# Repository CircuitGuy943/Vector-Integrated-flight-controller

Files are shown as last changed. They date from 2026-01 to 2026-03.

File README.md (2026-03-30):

I am currently trying to build my own drone from scratch, and slowly replace every component with my own, from creating fully custom PCBs for the flight controller or ESCs, to making a 3D printed drone chassis etc etc. And this is the fully fledged, multi functional, cool-looking flight controller. I present to you:

# *SABRE!*




For one of my biggest projects yet I designed a jack of all trades custom flight controller board. It also comes with custom firmware, or if possible compatibility with betaflight or other FC firmware out there. At it's core are two PCBs arranged in a stackup with the "top" and "bottom" sections. The two PCBs connect through the common 2.54mm pitch headers and stack on top of eachother and each serve to provide enough space for all the components and separate the sensitive digital components from the electromagnetic potential of the motor power rails. The bottom board houses E-Fuse protection and an INA226 current monitor to protect the boards, including powered FPV feed with the AT7456E and TX5813, accompanied by four MOSFET powered 12V LED strip channels. The top booard houses a powerful STM32F765VGT CPU which will, *fingers crossed,* be more than enough to run automatic flight levelling software quickly enough to not crash. Followed by a micro SD card slot for storing flight telemetry, programmable DIP switched for easy settings, BNO08x 9-DOF sensor module, segment display and pushbuttons for easy configuration without needing to reupload code and a BMP580 barometic sensor. More than I (or you) will ever need to fly a 4 blade, 1KG piece of PETG plastic :)

### Bottom Board:

Half of the bottom PCB houses the power delivery circuitry. This includes a dedicated TPS259850 chip, or an E-Fuse, required protection option for a drone that operates at around 20A sustained and 40A current peaks. Thanks to it's extremely low RDS on, basically no power is wasted, and it trips the circuit in a matter of microseconds when too much current is detected, which makes it extremely useful for a drone full of sensitive circuitry, compared to a traditional wire fuse. Followed by that is an INA226 chip, this aims to precisely monitor the current consumption of the entire drone, helping to predict flight times and efficiently manage battery health, through the use of a shunt resistor sized to the expected current draw. The current planes are optimized to make proper use of the different outer and inner layer thicknesses and properly distribute current with minimal heat up.

The other part of the bottom PCB houses the RF circuitry for the FPV system LED drivers togethor with power regulators that power the 12V rail for the LED drivers and the 5V rail for the FPV system and other 5V chips. The 12V power regulator (TPS55289) and the 5V regulator (TPS63070) both use the safest and most reliable layouts possible and are positioned to spatially divide the high ~32A currents on the bottom power distribution circuitry from the rest of the bottom board, a slide switch also controls the power supply to the TX5813 module, as this consumes the most out of the other board circuitry, at about ~200mA, this should help to increase flight time by cutting wasted power when the FPV function isn't being used. CSD16340 MOSFETS also serve to drive 4 seperate 12V LED strip channels, these I plan to connect to LED strips and create cool illuminations off of my drone.

The RF circuitry benefits from an impedance accurate JLC-3313 stackup and use of coplanar waveguide routing with via fencing, tearsrops and udnerpad via router to insure the least impedance mismatch possible. The actual RF system is composed of an external camera connector, or simple pin header (capable of reading almost any FPV camera such as the Caddx Ant Lite). The video signal is then passed through a meticulously routed 75ohm impedance matched trace into a MAX7456EUI (Or a newer drop in AT7456E replacement, pin to pin compatible), this module serves to inject an OSD (On screen display) into the video feed through communication with the STM32 MCU for easy sending of telemtry data like battery voltage, speed, altitude etc. The output from the OSD injection chip is then routed through another impedance matched trace with SAG correction into the video input of the TX5813. This modules handles the complicated circuitry of converting the video feed (~6MHz) into a radio signal of ~5.8GHz. That RF is then routed even more carefuly for the short length (~8mm) of the SMA launch into the SMA connector then into any respective 5.8GHz FPV antenna. (I also have a complemintary project for a 5.8GHz FPV reciever in another repository)

### Top Board:

Flying the drone is an STM32F765VGT CPU with up to 216MHz clock speed, hopefully resulting in almost perfect drone levelling and flight, on the other side of the board is also a USB C receptacle for programming the STM CPU, and powering the board while doing so (everything except the motors, of course, I also included diodes to prevent power backfeed). Close by is a BNO08x 9-DOF accelerometer, gyroscope and magnetometer, complete with an integrated 32-bit ARM Cortex-M0+ for quick sensor fusion with pre built firmware (meaning I have to code waaaay less :D). Motor PWM outputs for the ESCs also connected directly to PWM channels on the STM32 and two solder bridgeable connections to allow me to use the 5V supply from the ESCs in case my 5V regulator doesn't function properly under load (I've had bad experience with voltage regulators). Several voltage indicator LEDs are also placed near the USB C port at the back. Then there is also an UART FPC port designed to connect to a separate GPS board (large board for good GPS recieving power, check my other repositories) on the left side of the board. A 7 segment, 4 digit bitbanged display and several tactile pushbottoms also occupy the centre of the board, quite useless but they might be useful in changing more accute settings without having to reupload firmware every time. A micro SD card also connects through 4 channel SPI to STM32, I plan to use this to store settings or flight telemetry information that I could analyze while debugging. Powering all that is a 3.3V regulator (LMR51430XF), simplest (and therefore most reliable) I could find. And several other breakout headers for power/functionality. PWM inputs from the radio remote is recieved through a 3x8 header pinout designed for my specific radio reciever module.

(For BP reviewer: Btw, the two boards will be connected and bought as one piece from JLC, then I will cut them apart and stack them, I just ran out of time to do that, there's also quite a bit off polishing off to do like doing Fusion renders but I've also run out of time, so the project would be a bit more polished and it will be but not before the BP deadline. 3D file of board is also too big (over 100MB) to upload to GitHub)

## Features:
- Fully integrated design:
	- Custom firmware uploadable
	- Power distribution and control in one place
	- Dual stacked PCB design
 	- No screw, no wire inter board connection

- Power
	- Extremely low RDS protection e-Fuse (us trip time)
 	- INA226 current and voltage monitoring
  	- Backup/calibration voltage divider monitoring
  	- Fully optimized current planes, 40A+ capability
  	- Firmware built in battery management and flight warning system
  	- Meticulously designed 5V, 12V and 3.3V switching voltage regulators
  	- Backup ESC 5V supply availible
  	- LED indicators for power rail status
  	- 4 channel driver for 12V LED strips
  	- Power switch for TX5813 module for longer flight times

- Fully integrated FPV support
	- MAX7456/AT7456E OSD injection into FPV feed
	- Channel switch ability
	- TX5813 RF launch module
	- Accurate and reliable RF design
 	- Designed for impedance matched JLC 3313 stackup
 
- Flight Control
	- USB C programming connection 
	- Powerful STM32F765VGT CPU
 	- MicroSD card slot (For inflight telemtry storage)
  	- Programmable DIP switches
  	- Display/pushbuttons for setting adjustment without code reupload
  	- BNO08x 9-DOF sensor module with built in sensor fusion
  	- BMP580 Barometric sensor
  	- UART FPC connection for external GPS board
  	- Extra power and I2C debug headers
  	- 7 input PWM channels
  	- 4 ESC output PWM channels

## PCB
This is the PCB, with L1 to L4 Layers, silkscreen for both layers and an all layers view

PCB PCB 2 PCB 3 
PCB 4 PCB 5 PCB 6
PCB 7 PCB 8 PCB 9 

And here is the schematic

Schematic1
Schematic2
Schematic3

## 3D render
Here is also a 3D render to show off the PCB :)

Render1

## Firmware Overview
I've included some basic firmware (**untested**) that should get the TFT display working out of the box with a quick upload from arduino IDE

## BOM:
The BOM list for the actual PCB components is in the BOM folder section and here is also a BOM list for all the other components I plan to buy for this:

- PCB             $378.08		
- Antenna         $7.77      https://www.aliexpress.com/item/1005006153683653.html		
- 90 degree SMA   $4.51      https://www.aliexpress.com/item/1005005665998117.html						
- TX5813 module   $15.82     https://www.aliexpress.com/item/1005011698073364.html
											
Total			      $406.18

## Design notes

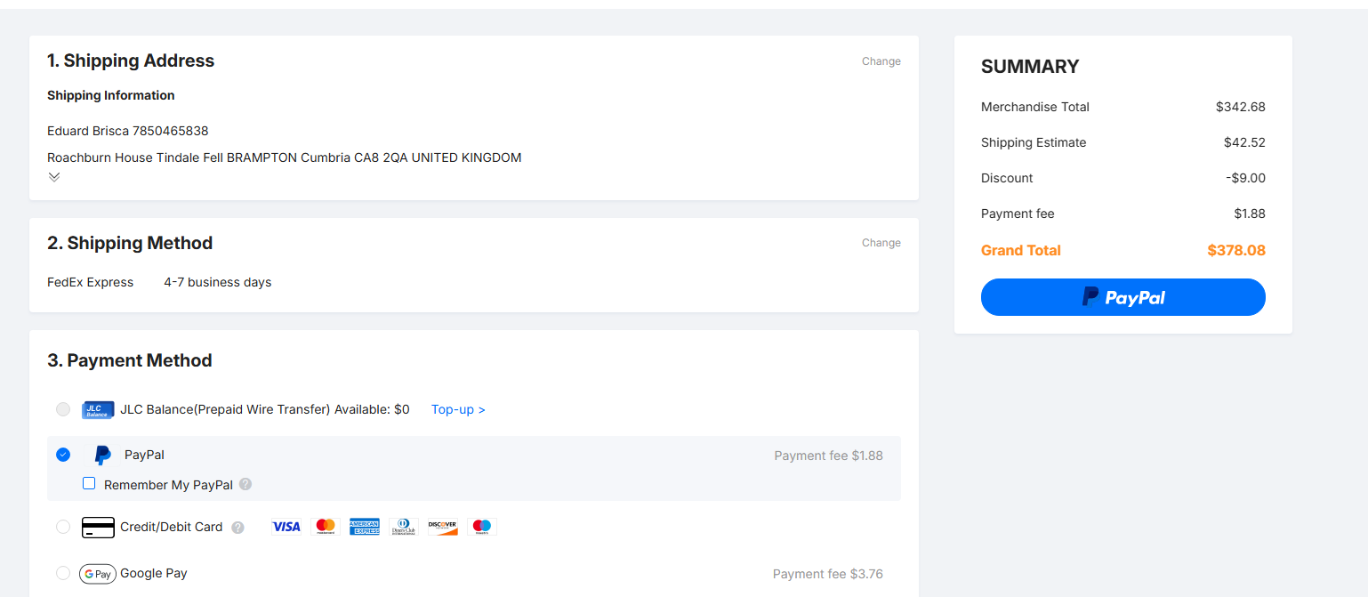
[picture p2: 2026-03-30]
Pictures/cart2.png

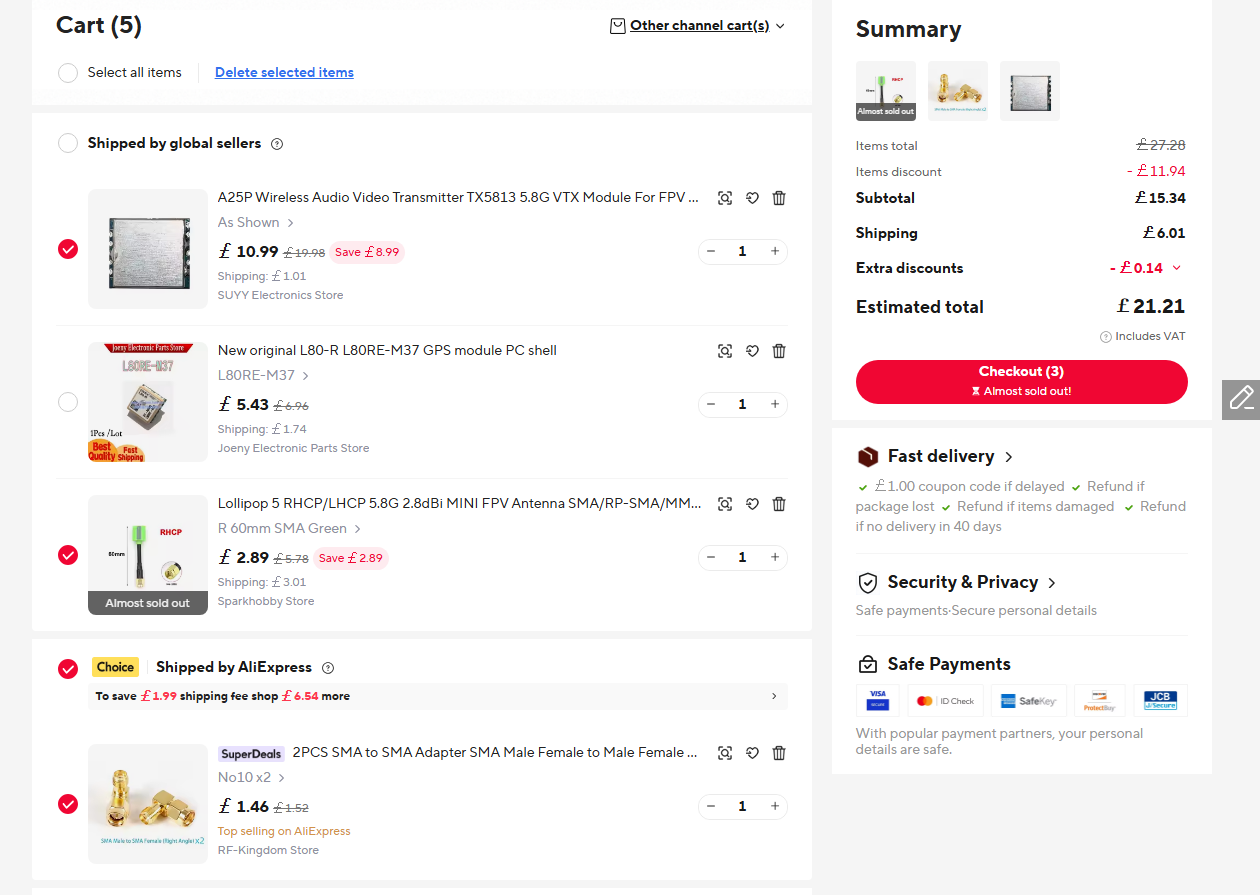
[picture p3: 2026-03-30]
Pictures/cart1.png

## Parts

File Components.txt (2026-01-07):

SENSORS
1. 9 Axis DOF IMU - BNO085. Sensor fusion integrated into the chip, reduces the need for MCU Kalman filters etc and therefore reduces MCU load and increases reliability
2. Barometer for altitude / temperature - BMP580. Can be connected straight to MCU or through a passthrough for “Environmental Sensors” through the BNO085, this is harder to implement but it may simplify circuitry use less I2C lines.
3. STM32 processor. Which one? Needs to be dual core

CONTROL
1. GPIO PWM outputs connected to 4 (more if there is space) groups of 3 pin headers for the ESCs, backup 5V power will also be taken from here as ESCs also step-down power to 5V. Located preferably in a symmetric position or spread out symmetrically so all the wires are extended the same.
2. PWM Inputs from the Radio Receiver (6 groups of also 3 pin headers, more if there is space and GPIO availability). These must OUTPUT 5V as well because the receiver needs a voltage input to function, unlike the ESCs that make their own.

POWER
1. USB C port connection on the back of the board
2. Female XT60 power connector with appropriate step down for MCU and sensors (Not LDO as components will likely consume too much current for too high a step down from ~14V)
3. Dual connection with diodes to both the ESC power outputs but also a voltage reducer like LDO or buck reducer on the USB C for redundancy if the LDO/buck dies.
4. Each side of the board will also have 2 (Maybe more if there's space) XT60 connectors powering the ESCs/motors

CAMERA SUPPORT
1. Caddx Ant (Lite) camera
2. 75-ohm impedance matched trace from JST-SH 1.0?mm connector to VID_IN of OSD Injector
3. MAX7456 OSD injector connected through communication protocol to MCU
4. MAC7456 VID_OUT connected through another 75-ohm impedance matched trace to TX5813 VID_IN
5. TX5813 SMD VTX + necessary support electronics + switch for on/off as VTX is very power hungry
6. 50-ohm impedance matched / ground trace from ANTENNA pad to an SMA connector
7. Antenna
Plus, appropriate ground plane and distances from other electronics such as MCU and switching regulators

OTHER
1. 12V LED control with up to 200mA+ of power available from GPIO.
2. SD Card module also placed wherever best, far away from the VTX module and preferably close to the MCU
3. I2C and SPI output headers for any future addition of sensors/logging/modules
4. 4 segment display (3 if not enough GPIO) plus a few tactile buttons (again GPIO limited) to allow easy tweaking of PID control values and other settings without the need for reupload of code.
5. Voltage divider for voltage sensing.
6. Voltage and current sensing on main power rail

USE 0805 LEDS FOR BASIC COMPONENT

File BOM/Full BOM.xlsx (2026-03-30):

BOM LIST | Pounds | Dollars
PCB |  | $378.08
Antenna | £5.80 | $7.77 | https://www.aliexpress.com/item/1005006153683653.html
90 degree SMA | £3.37 | $4.51 | https://www.aliexpress.com/item/1005005665998117.html
RX5808 module |  | $15.82 | https://www.aliexpress.com/item/1005011698073364.html
Total |  | $406.18

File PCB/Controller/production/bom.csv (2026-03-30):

Designator | Footprint | Quantity | Value | LCSC Part #
BUZ1 | BUZ-SMD_L9.0-W9.0-P8.00-LS9.3 | 1 | CPT-9019S-SMT-TR | C95163
C1 | 0603 | 1 | 0.1uF
C10, C57, C58 | 0402 | 3 | 2.2uF
C11, C14, C15, C2, C27, C29, C30, C31, C32, C33, C34, C36, C37, C38, C41, C44, C45, C46, C47, C48, C49, C50, C51, C63, C64, C67, C78 | 0402 | 27 | 100nF
C12, C13 | 0603 | 2 | 22uF
C16, C19, C20, C21, C22 | 0402 | 5 | 22uF
C17 | 0402 | 1 | 4.7uF
C18, C28 | 0402 | 2 | 22nF
C23 | 0402 | 1 | 3300pF
C24 | 0402 | 1 | 330pF
C25 | CAP-SMD_BD6.3-L6.6-W6.6-LS7.2-FD | 1 | 47uF | C970677
C3, C6 | 0603 | 2 | 10uF
C35, C43, C56, C68, C77 | 0402 | 5 | 10uF
C39, C40, C60, C61 | 0402 | 4 | 20pF
C4, C5 | 0805 | 2 | 10uF
C42, C74 | CAP-SMD_BD4.0-L4.3-W4.3-FD-LS5.3 | 2 | RVT1C220M0405_C3356_22uF | C3356
C52, C53, C54, C55, C65 | 0402 | 5 | 1uF
C59, C62 | 0402 | 2 | 6.8pF
C66 | 1210 | 1 | 100uF
C69, C75, C76 | 0402 | 3 | 0.1uF
C7, C8, C9 | 0805 | 3 | 22uF
C70 | 0402 | 1 | 15nF
C71 | 0402 | 1 | 3.3nF
C72 | 0402 | 1 | 10nF
C73 | 0402 | 1 | 150pF
C79 | 1206 | 1 | 22uF
CARD2 | TF-SMD_TF-01A | 1 | TF-01A | C91145
CN1 | AMASS_XT60PW-M_1x02_P7.20mm_Horizontal | 1 | XT60PW_M | C98732
CN2, CN4, CN5, CN6 | AMASS_XT60PW-F_1x02_P7.20mm_Horizontal | 4 | XT60PW_F | C428722
D1, D2, D3, D4, D5, D6 | D_SMA | 6 | SS34
GPS | FPC-SMD_6P-P0.50_XUNPU_FPC-05F-6PH20 | 1 | FPC-05F-6PH20 | C2856796
J1 | PinHeader_2x07_P2.54mm_Vertical | 1 | Conn_02x07_Odd_Even
J10, J5, J6, J7, J8 | PinHeader_1x03_P2.54mm_Vertical | 5 | Conn_01x03_Pin
J12 | PinHeader_2x02_P2.54mm_Vertical | 1 | Conn_02x02_Top_Bottom
J13, J18 | PinHeader_1x14_P2.54mm_Vertical | 2 | Conn_01x14_Pin
J14, J19 | PinHeader_1x06_P2.54mm_Vertical | 2 | Conn_01x06_Pin
J15, J20 | PinSocket_1x14_P2.54mm_Vertical | 2 | Conn_01x14_Socket
J16, J17 | PinSocket_1x06_P2.54mm_Vertical | 2 | Conn_01x06_Socket
J2, J9 | PinHeader_1x02_P1.00mm_Vertical | 2 | Conn_01x02_Pin
J21 | PinHeader_2x04_P2.54mm_Vertical | 1 | Conn_02x04_Odd_Even
L1 | IND-SMD_L4.0-W4.0-A | 1 | XFL4020-152MEC | C3033018
L2 | L0603 | 1 | FCM1608KF-601T03 | C141723
LED1 | LED-SEG-TH_14P-L32.2-W10.2-P2.54-S7.62-BL | 1 | FJ2481CH | C10707
LED11, LED12, LED13, LED14, LED15, LED16, LED2, LED9 | LED0603-RD | 8 | KT-0603YG | C2289
LED3, LED8 | LED0603-RD | 2 | KT-0603R | C2286
LED4, LED5, LED6, LED7 | LED0603-R-RD_WHITE | 4 | KT-0603W | C2290
Q1, Q2, Q3, Q5 | VSON-CLIP-8_L3.3-W3.3-P0.65-BL | 4 | CSD16340Q3 | C47616
Q10, Q7, Q8, Q9 | SOT-23_L2.9-W1.3-P1.90-LS2.4-BR | 4 | LBSS138LT1G | C8490
R1, R2 | 0402 | 2 | 5.1K
R10 | 0402 | 1 | 22.1K
R100, R103, R104, R16, R99 | 0402 | 5 | 4.7K
R101 | 0603 | 1 | 10K
R102, R12, R20, R22, R27, R28, R29, R30, R31, R34, R35, R49, R58, R6, R61, R62, R63, R64, R65, R66, R7, R88, R96, R97, R98 | 0402 | 25 | 10K
R11, R33 | 0402 | 2 | 68K
R13, R14 | 0402 | 2 | 56K
R15, R52 | 0402 | 2 | 24K
R17, R18, R19, R21, R36, R37, R38, R39, R4, R40, R41, R42, R43, R44, R45, R46, R47, R48, R60, R67, R68, R69, R76, R77, R82 | 0402 | 25 | 220
R23 | 0402 | 1 | 150K
R24 | 0402 | 1 | 47K
R25, R26, R55 | 0402 | 3 | 2.2K
R3 | R2725 | 1 | HOLR2725D-4W-2MR-1% | C500746
R32, R54, R85, R86, R87 | 0402 | 5 | 1K
R5, R72, R73, R74, R75 | 0402 | 5 | 680
R50 | 0402 | 1 | 160
R51 | 0402 | 1 | 1.1K
R53 | 0402 | 1 | 1.5K
R56 | 0402 | 1 | 50K
R78 | 0402 | 1 | 100
R8, R9 | 0402 | 2 | 100K
R83, R84 | 0603 | 2 | 75
SW1, SW11, SW12, SW2, SW3, SW4, SW5, SW6, SW7, SW8, SW9 | SW-SMD_L3.9-W3.0-P4.45 | 11 | TS-1088-AR02016 | C720477
SW10, SW14 | SW-SMD_DSIC03LSGET | 2 | DSIC03LSGET | C57453
SW13 | SW-SMD_MK-11C04-G013 | 1 | MK-11C04-G013 | C778185
U1 | LQFP-100_14x14mm_P0.5mm | 1 | STM32F765VGTx
U10 | MC7RE | 1 | ~
U11 | VSSOP-10_L3.0-W3.0-P0.50-LS4.9-BL | 1 | INA226AQDGSRQ1 | C2653835
U12 | SOT-23-6 | 1 | LMR51430XF
U13 | CAP-SMD_BD6.3-L6.6-W6.6-LS7.2-FD-1 | 1 | 100uF | C970685
U14 | LGA-8_BME280_BL | 1 | BME280 | C92489
U15 | CRYSTAL-SMD_4P-L3.2-W2.5-BL | 1 | S322527M20PF10PPM | C7420779
U16 | VQFN-20_L4.5-W3.5-P0.50-BL-EP | 1 | TXB0108RGYR | C194701
U17 | TX5813 | 1 | TX5813
U19 | QFN-26_L5.0-W4.5_TPS259850RQPR | 1 | TPS259850RQPR | C6290347
U2 | LGA-28_L5.2-W3.8-P0.50-BL-1 | 1 | BNO080 | C717991
U20 | SO-8_L4.9-W3.9-P1.27-LS6.0-BL | 1 | LD1117D33TR | C2971297
U3 | LGA-10_L2.0-W2.0-P0.50-TL_BMP580 | 1 | BMP580 | C22391138
U4 | IND-SMD_L5.5-W5.3 | 1 | XAL5050-562MEC | C7305309
U5 | HTSSOP-28_L9.7-W4.4-P0.65-LS6.4-BL-EP5.5 | 1 | MAX7456EUI | C5346361
U6 | SMA-TH_SMA-KWE_C7498154 | 1 | SMA_Conn | C7498154
U7 | VQFN-21_L5.0-W3.0-P0.50-TL | 1 | TPS55289RYQR | C5942077
U8 | IND-SMD_L7.5-W7.2-1 | 1 | XAL7070-472MEC | C3911513
U9 | VQFN-15_L3.0-W2.5-P0.50-BL | 1 | TPS630701RNMT | C181473
USB1 | USB-C-SMD_TYPE-C16PIN_C668624 | 1 | TYPE-C 16P(073) | C668624
X1 | CRYSTAL-SMD_4P-L3.2-W2.5-BL | 1 | X322525MOB4SI | C9006
X2 | FC-135R_L3.2-W1.5 | 1 | Q13FC1350000400 | C32346

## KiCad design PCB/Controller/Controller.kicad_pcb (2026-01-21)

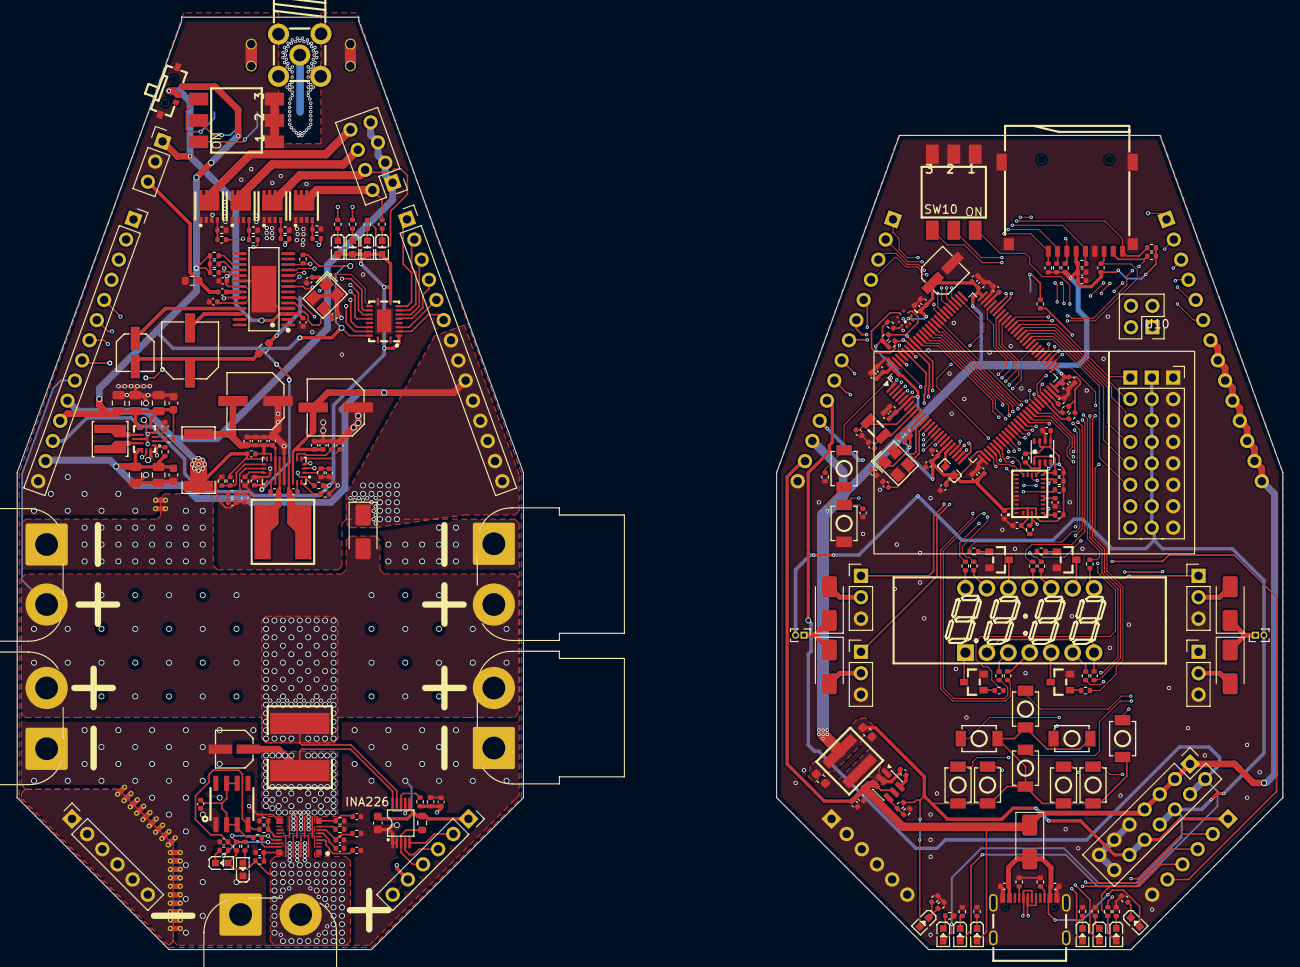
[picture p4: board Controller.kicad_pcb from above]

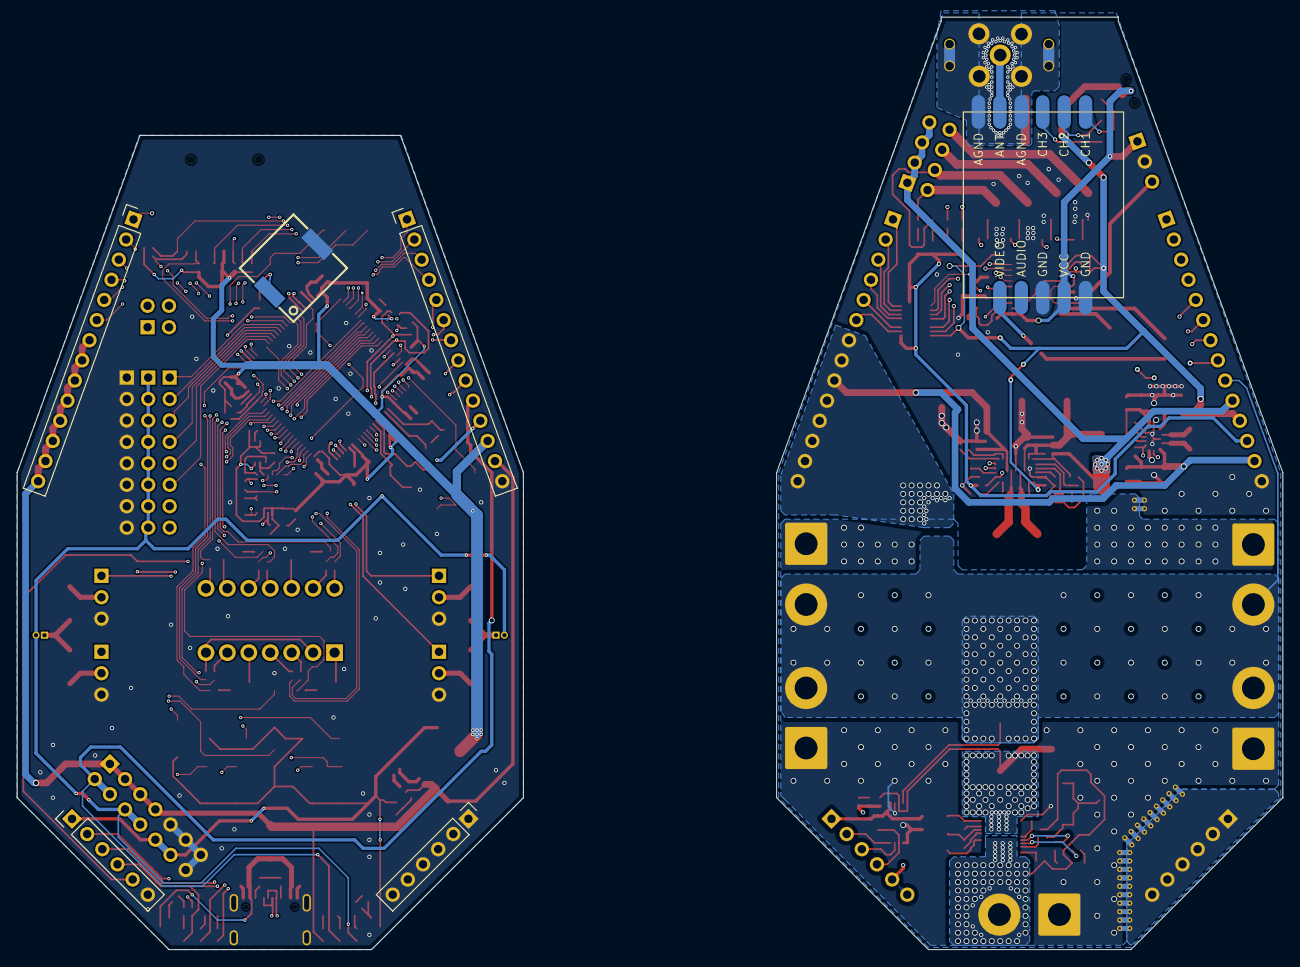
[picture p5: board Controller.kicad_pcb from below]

Board: 4 copper layers, 150.0 x 110.5 mm, 284 parts (6 on the bottom side), 219 nets.

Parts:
BUZ1: CPT-9019S-SMT-TR; BUZ-SMD_L9.0-W9.0-P8.00-LS9.3
C1: 0.1uF; C_0603_1608Metric
C2, C11, C14, C15, C26, C27, C29, C30, C31, C32, C33, C34, C36, C37, C38, C41, C44, C45, C46, C47, C48, C49, C50, C51, C63, C64, C67, C78: 100nF; C_0402_1005Metric
C3, C6: 10uF; C_0603_1608Metric
C4, C5: 10uF; C_0805_2012Metric
C7, C8, C9: 22uF; C_0805_2012Metric
C10, C57, C58: 2.2uF; C_0402_1005Metric
C12, C13: 22uF; C_0603_1608Metric
C16, C19, C20, C21, C22: 22uF; C_0402_1005Metric
C17: 4.7uF; C_0402_1005Metric
C18, C28: 22nF; C_0402_1005Metric
C23: 3300pF; C_0402_1005Metric
C24: 330pF; C_0402_1005Metric
C25: 47uF; CAP-SMD_BD6.3-L6.6-W6.6-LS7.2-FD
C35, C43, C56, C68, C77: 10uF; C_0402_1005Metric
C39, C40, C60, C61: 20pF; C_0402_1005Metric
C42, C66, C74: RVT1C220M0405_C3356_22uF; CAP-SMD_BD4.0-L4.3-W4.3-FD-LS5.3
C52, C53, C54, C55, C65: 1uF; C_0402_1005Metric
C59, C62: 6.8pF; C_0402_1005Metric
C69, C75, C76: 0.1uF; C_0402_1005Metric
C70: 15nF; C_0402_1005Metric
C71: 3.3nF; C_0402_1005Metric
C72: 10nF; C_0402_1005Metric
C73: 150pF; C_0402_1005Metric
CN1: XT60PW_M; AMASS_XT60PW-M_1x02_P7.20mm_Horizontal
CN2, CN4, CN5, CN6: XT60PW_F; AMASS_XT60PW-F_1x02_P7.20mm_Horizontal
Card2: TF-01A; TF-SMD_TF-01A
D1, D2, D3, D4, D5, D6: SS34; D_SMA
J1: Conn_02x07_Odd_Even; PinHeader_2x07_P2.54mm_Vertical
J2, J9: Conn_01x02_Pin; PinHeader_1x02_P1.00mm_Vertical
J5, J6, J7, J8, J10: Conn_01x03_Pin; PinHeader_1x03_P2.54mm_Vertical
J12: Conn_02x02_Top_Bottom; PinHeader_2x02_P2.54mm_Vertical
J13, J18: Conn_01x14_Pin; PinHeader_1x14_P2.54mm_Vertical
J14, J19: Conn_01x06_Pin; PinHeader_1x06_P2.54mm_Vertical
J15, J20: Conn_01x14_Socket; PinSocket_1x14_P2.54mm_Vertical
J16, J17: Conn_01x06_Socket; PinSocket_1x06_P2.54mm_Vertical
J21: Conn_02x04_Odd_Even; PinHeader_2x04_P2.54mm_Vertical
L1: XFL4020-152MEC; IND-SMD_L4.0-W4.0-A
L2: FCM1608KF-601T03; L0603
LED1: FJ2481CH; LED-SEG-TH_14P-L32.2-W10.2-P2.54-S7.62-BL
LED2, LED9, LED11, LED12, LED13, LED14, LED15, LED16: KT-0603YG; LED0603-RD
LED3, LED8: KT-0603R; LED0603-RD
LED4, LED5, LED6, LED7: KT-0603W; LED0603-R-RD_WHITE
NT1, NT7, NT8, NT9, NT10, NT10#2, NT10#3, NT10#4, NT11, NT11#2, NT11#3, NT11#4, NT12, NT13, NT13#2, NT13#3, NT14, NT15, NT15#2, NT15#3, NT16: NetTie_2; NetTie-2_THT_Pad0.3mm
NT2, NT17: NetTie_2; NetTie-2_THT_Pad1.0mm
Q1, Q2, Q3, Q5: CSD16340Q3; VSON-CLIP-8_L3.3-W3.3-P0.65-BL
Q7, Q8, Q9, Q10: LBSS138LT1G; SOT-23_L2.9-W1.3-P1.90-LS2.4-BR
R1, R2: 5.1K; R_0402_1005Metric
R3: HOLR2725D-4W-2MR-1%; R2725
R4, R17, R18, R19, R21, R36, R37, R38, R39, R40, R41, R42, R43, R44, R45, R46, R47, R48, R60, R67, R68, R69, R76, R77, R82: 220; R_0402_1005Metric
R5, R72, R73, R74, R75: 680; R_0402_1005Metric
R6, R7, R12, R20, R22, R27, R28, R29, R30, R31, R34, R35, R49, R58, R61, R62, R63, R64, R65, R66, R88, R96, R97, R98, R102: 10K; R_0402_1005Metric
R8, R9: 100K; R_0402_1005Metric
R10: 22.1K; R_0402_1005Metric
R11, R33: 68K; R_0402_1005Metric
R13, R14: 56K; R_0402_1005Metric
R15: MS122WF100MT4E; R2512
R16, R99, R100, R103, R104: 4.7K; R_0402_1005Metric
R23: 150K; R_0402_1005Metric
R24: 47K; R_0402_1005Metric
R25, R26, R55: 2.2K; R_0402_1005Metric
R32, R54, R85, R86, R87: 1K; R_0402_1005Metric
R50: 160; R_0402_1005Metric
R51: 1.1K; R_0402_1005Metric
R52: 48K; R_0402_1005Metric
R53: 1.5K; R_0402_1005Metric
R56: 50K; R_0402_1005Metric
R78: 100; R_0402_1005Metric
R83, R84: 75; R_0603_1608Metric
R101: 10K; R_0603_1608Metric
SW1, SW2, SW3, SW4, SW5, SW6, SW7, SW8, SW9, SW11, SW12: TS-1088-AR02016; SW-SMD_L3.9-W3.0-P4.45
SW10, SW14: DSIC03LSGET; SW-SMD_DSIC03LSGET
SW13: MK-11C04-G013; SW-SMD_MK-11C04-G013
U1: STM32F765VGTx; LQFP-100_14x14mm_P0.5mm
U2: BNO080; LGA-28_L5.2-W3.8-P0.50-BL-1
U3: BMP580; LGA-10_L2.0-W2.0-P0.50-TL_BMP580
U4: XAL5050-562MEC; IND-SMD_L5.5-W5.3
U5: MAX7456EUI; HTSSOP-28_L9.7-W4.4-P0.65-LS6.4-BL-EP5.5
U6: SMA_Conn; SMA-TH_SMA-KWE_C7498154
U7: TPS55289RYQR; VQFN-21_L5.0-W3.0-P0.50-TL
U8: XAL7070-472MEC; IND-SMD_L7.5-W7.2-1
U9: TPS630701RNMT; VQFN-15_L3.0-W2.5-P0.50-BL
U10: MC7RE
U11: INA226AQDGSRQ1; VSSOP-10_L3.0-W3.0-P0.50-LS4.9-BL
U12: LMR51430; SOT-23-6
U13, U18: 100uF; CAP-SMD_BD6.3-L6.6-W6.6-LS7.2-FD-1
U14: BME280; LGA-8_BME280_BL
U15: S322527M20PF10PPM; CRYSTAL-SMD_4P-L3.2-W2.5-BL
U16: TXB0108RGYR; VQFN-20_L4.5-W3.5-P0.50-BL-EP
U17: TX5813
U19: TPS259850RQPR; QFN-26_L5.0-W4.5_TPS259850RQPR
U20: LD1117D33TR; SO-8_L4.9-W3.9-P1.27-LS6.0-BL
USB1: TYPE-C 16P(073); USB-C-SMD_TYPE-C16PIN_C668624
X1: X322525MOB4SI; CRYSTAL-SMD_4P-L3.2-W2.5-BL
X2: Q13FC1350000400; FC-135R_L3.2-W1.5

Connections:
+3.3V: C12.2, C13.2, C29.1, C30.1, C32.2, C33.2, C34.2, C42.1, C43.1, C45.1, C46.1, C47.1, C48.1, C49.1, C50.1, C51.1, C52.1, C53.1, C54.1, C55.1, C56.1, C64.1, C65.1, C67.1, C68.1, Card2.4 (VDD), J1.10, J1.12, J13.12, J14.1, L2.2, LED16.2 (A), R6.2, R9.2, R25.2, R26.2, R27.1, R58.2, R61.2, R62.2, R63.2, R64.2, R65.2, R66.2, R96.1, R97.1, R98.1, R99.1, R100.1, R102.1, R103.2, R104.2, SW1.2, SW2.2, SW3.2, SW4.2, SW5.2, SW6.2, SW7.2, SW8.2, SW9.2, SW12.1, U1.6 (VBAT), U1.11 (VDD), U1.20 (VREF+), U1.27 (VDD), U1.50 (VDD), U1.75 (VDD), U1.100 (VDD), U2.3 (VDD), U2.5 (PS1), U2.28 (VDDIO), U3.1 (VDDIO), U3.10 (VDD), U4.2, U14.2 (CSB), U14.6 (VDDIO), U14.8 (VDD)
+3.3V_B: C1.2, J15.12, J16.1, LED4.1 (A), LED5.1 (A), LED6.1 (A), LED7.1 (A), R28.1, R101.2, U11.6 (VS+), U16.2 (VCCA), U16.10 (OE)
+5V: J1.6, J1.8, J2.2, J9.2, J13.11, LED15.2 (A), U10.17 (5V), U10.18 (5V), U10.19 (5V), U10.20 (5V), U10.21 (5V), U10.22 (5V), U10.23 (5V), U10.24 (SBUS3)
+5V_B: C6.2, C7.2, C8.2, C9.2, C17.2, J15.11, R8.2, R85.2, R86.2, R87.2, R88.2, SW13.1, U7.18 (VCC), U9.5 (FB), U9.7 (VOUT), U16.19 (VCCB)
+12V: J1.2, J1.4, J13.10, LED14.2 (A)
+12V_B: C26.1, J15.10, J21.1, J21.3, J21.5, J21.7, R11.2, R15.2, U7.13 (ISN)
BMP580_INT: R102.2, U1.96 (PB9), U3.7 (INT)
BNO580_BOOTN: R27.2, U1.34 (PB0), U2.4 (BOOTN)
BNO580_CSN: U1.77 (PA15), U2.18 (H_CSN)
BNO580_INTN: R98.2, U1.33 (PC5), U2.14 (H_INTN)
BNO580_MISO: U1.30 (PA6), U2.20 (H_SDA/H_MISO/TX)
BNO580_MOSI: U1.31 (PA7), U2.17 (SA0/H_MOSI)
BNO580_NRST: R97.2, U1.32 (PC4), U2.11 (NRST)
BNO580_SCLK: U1.29 (PA5), U2.19 (H_SCL/SCK/RX)
BNO580_WAKE: R96.2, U1.35 (PB1), U2.6 (PS0/WAKE)
BOOT: R22.1, SW12.2, U1.94 (BOOT0)
BOOT1: C14.2, U7.8 (SW1), U8.2
BOOT2: C15.2, U7.10 (SW2), U8.1
BUTTON_DECREASE: SW4.1, U1.39 (PE9)
BUTTON_F1: SW6.1, U1.41 (PE11)
BUTTON_F2: SW7.1, U1.42 (PE12)
BUTTON_F3: SW8.1, U1.43 (PE13)
BUTTON_F4: SW9.1, U1.51 (PB12)
BUTTON_INCREASE: SW3.1, U1.38 (PE8)
BUTTON_LEFT: SW1.1, U1.36 (PB2)
BUTTON_OK: SW5.1, U1.40 (PE10)
BUTTON_RIGHT: SW2.1, U1.37 (PE7)
BUZZER: R78.1, U1.53 (PB14)
DIP_1: SW10.6 (B1), U1.52 (PB13)
DIP_2: SW10.5 (B2), U1.54 (PB15)
DIP_3: SW10.4 (B3), U1.55 (PD8)
DISP_A: R41.2, U1.87 (PD6)
DISP_B: R44.2, U1.86 (PD5)
DISP_C: R38.2, U1.85 (PD4)
DISP_D: R39.2, U1.84 (PD3)
DISP_D2D1: R45.2, U1.58 (PD11)
DISP_DIG1: R46.1, U1.91 (PB5)
DISP_DIG2: R48.1, U1.90 (PB4)
DISP_DIG3: R36.1, U1.89 (PB3)
DISP_DIG4: R47.1, U1.88 (PD7)
DISP_DP: R40.2, U1.67 (PA8)
DISP_E: R37.2, U1.72 (PA13)
DISP_F: R42.2, U1.69 (PA10)
DISP_G: R43.2, U1.68 (PA9)
EXTRA_I2C_EN: J12.4, U1.44 (PE14)
EXTRA_I2C_INT: J12.3, U1.45 (PE15)
EXTRA_I2C_SCL: J12.1, R103.1, U1.46 (PB10)
EXTRA_I2C_SDA: J12.2, R104.1, U1.47 (PB11)
GND: BUZ1.2 (-), C10.2, C12.1, C13.1, C29.2, C30.2, C31.1, C32.1, C33.1, C34.1, C35.2, C42.2, C43.2, C45.2, C46.2, C47.2, C48.2, C49.2, C50.2, C51.2, C52.2, C53.2, C54.2, C55.2, C56.2, C57.1, C58.1, C59.2, C60.2, C61.1, C62.2, C63.2, C64.2, C65.2, C67.2, C68.2, C77.2, C78.2, Card2.6 (VSS), Card2.10 (GND), Card2.11 (GND), Card2.12 (GND), Card2.13 (GND), J1.9, J1.11, J1.13, J1.14, J5.3, J6.3, J7.3, J8.3, J13.14, J14.6, J19.1, J19.2, J19.3, J19.4, J19.5, J19.6, Q7.2 (S), Q8.2 (S), Q9.2 (S), Q10.2 (S), R1.2, R2.2, R4.2, R5.2, R10.2, R22.2, R72.2, R73.2, R74.2, R75.2, R76.2, R77.2, R82.2, SW10.1 (A1), SW10.2 (A2), SW10.3 (A3), SW11.1, U1.10 (VSS), U1.19 (VSSA), U1.26 (VSS), U1.49 (VSS), U1.74 (VSS), U1.99 (VSS), U2.2 (GND), U2.25 (GND), U2.26 (XOUT32/CLKSEL1), U3.3 (VSS), U3.5 (SDO), U3.6 (CSB), U3.8 (VSS), U3.9 (VSS), U10.9 (GND), U10.10 (GND), U10.11 (GND), U10.12 (GND), U10.13 (GND), U10.14 (GND), U10.15 (GND), U10.16 (SBUS2), U12.1 (GND), U14.1 (GND), U14.7 (GND), USB1.1 (SHELL), USB1.2 (SHELL), USB1.3 (SHELL), USB1.4 (SHELL), USB1.A1B12 (GND), USB1.B1A12 (GND), X1.2 (GND), X1.4 (GND)
GND_B: C2.2, C3.1, C4.1, C5.1, C6.1, C7.1, C8.1, C9.1, C16.1, C17.1, C18.1, C19.1, C20.1, C21.1, C22.1, C23.1, C24.1, C25.1, C27.1, C36.1, C37.1, C38.1, C39.2, C40.1, C44.2, J10.2, J15.14, J16.6, J17.1, J17.2, J17.3, J17.4, J17.5, J17.6, NT1.1, NT2.2, NT7.1, NT8.1, NT9.1, NT10.1, NT10#2.1, NT10#3.1, NT10#4.1, NT11.1, NT11#2.1, NT11#3.1, NT11#4.1, NT12.1, NT13.1, NT13#2.1, NT13#3.1, NT14.1, NT15.1, NT15#2.1, NT15#3.1, NT16.1, NT17.2, Q1.1 (S), Q1.2 (S), Q1.3 (S), Q2.1 (S), Q2.2 (S), Q2.3 (S), Q3.1 (S), Q3.2 (S), Q3.3 (S), Q5.1 (S), Q5.2 (S), Q5.3 (S), R13.1, R14.2, R16.1, R20.2, R29.1, R30.1, R31.1, R34.1, R35.1, R83.2, SW13.4, SW13.5, SW14.1 (A1), SW14.2 (A2), SW14.3 (A3), U5.4 (DGND), U5.20 (AGND), U5.23 (PGND), U5.29 (EP), U7.9 (PGND), U7.17 (AGND), U9.4 (GND), U9.6 (FB2), U9.10 (PGND), U9.15 (VSEL), U13.1, U15.2 (GND), U15.4 (GND), U16.11 (GND), U16.21 (EP), U17.9 (GND), U17.11 (GND)
HSE_IN: C61.2, U1.12 (PH0), X1.1 (OSC1)
HSE_OUT: C60.1, U1.13 (PH1), X1.3 (OSC2)
INA_ALERT_B: J16.4, R101.1, U11.3 (Alert)
INA_ALERT_T: J14.4, LED3.2 (A), R6.1, U1.95 (PB8)
LED1_POWER: J21.8, Q1.5 (D), Q1.6 (D), Q1.7 (D), Q1.8 (D), R67.2
LED1_PWM_B: J15.1, R17.2
LED1_PWM_T: J13.1, U1.15 (PC0)
LED2_POWER: J21.6, Q2.5 (D), Q2.6 (D), Q2.7 (D), Q2.8 (D), R60.2
LED2_PWM_B: J15.2, R18.2
LED2_PWM_T: J13.2, U1.16 (PC1)
LED3_POWER: J21.4, Q5.5 (D), Q5.6 (D), Q5.7 (D), Q5.8 (D), R68.2
LED3_PWM_B: J15.3, R21.2
LED3_PWM_T: J13.3, U1.17 (PC2)
LED4_POWER: J21.2, Q3.5 (D), Q3.6 (D), Q3.7 (D), Q3.8 (D), R69.2
LED4_PWM_B: J15.4, R19.2
LED4_PWM_T: J13.4, U1.18 (PC3)
LSE_IN: C59.1, U1.8 (PC14), X2.1
LSE_OUT: C62.1, U1.9 (PC15), X2.2
MAIN_SCK_B: J15.6, J16.2, U7.3 (SCL), U11.5 (SCL)
MAIN_SCK_T: J13.6, J14.2, R99.2, U1.92 (PB6), U3.2 (SCK)
MAIN_SDA_B: J15.7, J16.3, U7.4 (SDA), U11.4 (SDA)
MAIN_SDA_T: J13.7, J14.3, R100.2, U1.93 (PB7), U3.4 (SDI)
MAX7456_CS_3.3V_B: J20.4, U16.6 (A5)
MAX7456_CS_3.3V_T: J18.4, U1.3 (PE4)
MAX7456_CS_5V: U5.8 (~CS), U16.15 (B5)
MAX7456_HSYNC_5V: R87.1, U5.18 (~HSYNC)
MAX7456_LOS_3.3V_B: J20.5, U16.4 (A3)
MAX7456_LOS_3.3V_T: J18.5, U1.2 (PE3)
MAX7456_LOS_5V: R86.1, U5.12 (LOS), U16.17 (B3)
MAX7456_RESET_3.3V_B: J20.6, U16.3 (A2)
MAX7456_RESET_3.3V_T: J18.6, U1.98 (PE1)
MAX7456_RESET_5V: R88.1, U5.19 (~RESET), U16.18 (B2)
MAX7456_SCLK_3.3V_B: J20.1, U16.9 (A8)
MAX7456_SCLK_3.3V_T: J18.1, U1.1 (PE2)
MAX7456_SCLK_5V: U5.10 (SCLK), U16.12 (B8)
MAX7456_SDIN_3.3V_B: J20.2, U16.8 (A7)
MAX7456_SDIN_3.3V_T: J18.2, U1.5 (PE6)
MAX7456_SDIN_5V: U5.9 (SDIN), U16.13 (B7)
MAX7456_SDOUT_3.3V_B: J20.3, U16.7 (A6)
MAX7456_SDOUT_3.3V_T: J18.3, U1.4 (PE5)
MAX7456_SDOUT_5V: U5.11 (SDOUT), U16.14 (B6)
MAX7456_VSYNC_5V: R85.1, U5.17 (~VSYNC)
MGND_B: C1.1, C28.1, C69.1, C70.2, C71.2, C72.1, C73.1, C74.2, C75.1, C76.2, CN1.1 (-), CN2.2, CN4.2, CN5.2, CN6.2, LED9.1 (K), NT1.2, NT7.2, NT8.2, NT9.2, NT10.2, NT10#2.2, NT10#3.2, NT10#4.2, NT11.2, NT11#2.2, NT11#3.2, NT11#4.2, NT12.2, NT13.2, NT13#2.2, NT13#3.2, NT14.2, NT15.2, NT15#2.2, NT15#3.2, NT16.2, R24.2, R49.1, R50.1, R51.2, R52.2, U11.1 (A1), U11.2 (A0), U11.7 (GND), U19.14 (GND), U20.1 (ADJ/GND)
MOTOR_PWM1: J5.1, U1.22 (PA0)
MOTOR_PWM2: J6.1, U1.23 (PA1)
MOTOR_PWM3: J7.1, U1.24 (PA2)
MOTOR_PWM4: J8.1, U1.25 (PA3)
unnamed: BUZ1.1 (+), R78.2
unnamed: C24.2, R12.1
unnamed: C66.2, R84.2, U18.1
unnamed: C76.1, R56.1, U20.2 (VOUT), U20.3 (VOUT), U20.6 (VOUT), U20.7 (VOUT)
unnamed: C75.2, CN1.2 (+), LED8.2 (A), R32.2, R33.2, R55.1, U19.23 (VIN), U19.24 (VIN), U19.25 (VIN), U19.26 (VIN), U20.4 (VIN)
unnamed: D3.2 (A), J5.2
unnamed: D3.1 (K), D4.1 (K), J2.1
unnamed: D4.2 (A), J6.2
unnamed: D5.2 (A), J7.2
unnamed: D5.1 (K), D6.1 (K), J9.1
unnamed: D6.2 (A), J8.2
unnamed: LED1.14 (A), R42.1
unnamed: LED1.8 (B), R44.1
unnamed: LED1.6 (C), R38.1
unnamed: LED1.11 (D2D1), R41.1
unnamed: LED1.2 (D), LED1.7 (D), R39.1
unnamed: LED1.1 (DIG1), Q7.3 (D)
unnamed: LED1.12 (DIG2), Q10.3 (D)
unnamed: LED1.5 (DIG3), Q8.3 (D)
unnamed: LED1.9 (DIG4), Q9.3 (D)
unnamed: LED1.3 (DP), R40.1
unnamed: LED1.4 (E), R37.1
unnamed: LED1.13 (F), R45.1
unnamed: LED1.10 (G), R43.1
unnamed: LED2.1 (K), R72.1
unnamed: LED3.1 (K), R4.1
unnamed: LED4.2 (K), R67.1
unnamed: LED5.2 (K), R60.1
unnamed: LED6.2 (K), R68.1
unnamed: LED7.2 (K), R69.1
unnamed: LED8.1 (K), R53.1
unnamed: LED9.2 (A), R54.1
unnamed: LED11.1 (K), R5.1
unnamed: LED12.1 (K), R73.1
unnamed: LED13.1 (K), R74.1
unnamed: LED14.1 (K), R75.1
unnamed: LED15.1 (K), R76.1
unnamed: LED16.1 (K), R77.1, R82.1
unnamed: NT2.1, NT17.1, U6.1, U6.2, U6.3, U6.4, U17.1 (AGND), U17.3 (AGND)
unnamed: Q1.4 (G), R17.1, R29.2
unnamed: Q2.4 (G), R18.1, R30.2
unnamed: Q3.4 (G), R19.1, R34.2
unnamed: Q5.4 (G), R21.1, R31.2
unnamed: Q7.1 (G), R46.2
unnamed: Q8.1 (G), R36.2
unnamed: Q9.1 (G), R47.2
unnamed: Q10.1 (G), R48.2
unnamed: C57.2, U1.48 (VCAP_1)
unnamed: C58.2, U1.73 (VCAP_2)
unnamed: L2.1, U1.21 (VDDA)
unnamed: C31.2, U2.9 (CAP), U2.10 (CLKSEL0)
unnamed: C66.1, U5.25 (SAG)
unnamed: C41.2, U5.22 (VIN)
unnamed: U5.26 (VOUT), U18.2
unnamed: C14.1, U7.20 (BOOT1)
unnamed: C15.1, U7.19 (BOOT2)
unnamed: R13.2, U7.16 (CDC)
unnamed: C23.2, R12.2, U7.15 (COMP)
unnamed: C18.2, U7.5 (DITH/SYNC)
unnamed: R20.1, U7.21 (EXTVCC)
unnamed: R11.1, R16.2, U7.14 (FB/~INT)
unnamed: R14.1, U7.6 (FSW)
unnamed: C19.2, C20.2, C21.2, C22.2, C25.2, C26.2, R15.1, U7.11 (VOUT), U7.12 (ISP)
unnamed: C44.1, R35.2, U7.2 (MODE)
unnamed: R7.2, U9.1 (PS/S), U9.14 (EN)
unnamed: L1.1, U9.11 (L1)
unnamed: L1.2, U9.9 (L2)
unnamed: R8.1, U9.2 (PG)
unnamed: C2.1, U9.3 (VAUX)
unnamed: C11.1, U12.6 (CB)
unnamed: R9.1, R10.1, U12.4 (FB)
unnamed: C11.2, U4.1, U12.2 (SW)
unnamed: R26.1, U2.15 (ENV_SCL), U14.4 (SCK)
unnamed: R25.1, U2.16 (ENV_SDA), U14.3 (SDI)
unnamed: U6.5, U17.2 (ANT)
unnamed: C71.1, U19.4 (DVDT)
unnamed: R33.1, R49.2, U19.18 (EN/UVLO)
unnamed: R50.2, U19.8 (ILIM)
unnamed: C72.2, R51.1, U19.7 (IMON)
unnamed: C73.2, R52.1, U19.9 (IREF)
unnamed: C70.1, U19.6 (ITIMER)
unnamed: R54.2, R55.2, U19.19 (PG)
unnamed: R56.2, U19.21 (SWEN)
unnamed: C69.2, R32.1, U19.22 (VDD)
unnamed: R53.2, U19.20 (~FLT)
unnamed: R2.1, USB1.A5 (CC1)
unnamed: R1.1, USB1.B5 (CC2)
RADIO_PWM1: U1.64 (PC7), U10.1 (CH1)
RADIO_PWM2: U1.63 (PC6), U10.2 (CH2)
RADIO_PWM3: U1.62 (PD15), U10.3 (CH3)
RADIO_PWM4: U1.61 (PD14), U10.4 (CH4)
RADIO_PWM5: U1.60 (PD13), U10.5 (CH5)
RADIO_PWM6: U1.59 (PD12), U10.6 (CH6)
RESET: C63.1, SW11.2, U1.14 (NRST)
SD_CD: Card2.9 (CD), R58.1, U1.82 (PD1)
SD_CLK: Card2.5 (CLK(SCLK)), R64.1, U1.80 (PC12)
SD_CMD: Card2.3 (CMD(DI)), R65.1, U1.83 (PD2)
SD_DAT0: Card2.7 (DAT0(D0)), R63.1, U1.65 (PC8)
SD_DAT1: Card2.8 (DAT1(RSV)), R62.1, U1.66 (PC9)
SD_DAT2: Card2.1 (DAT2(RSV)), R61.1, U1.78 (PC10)
SD_DAT3: Card2.2 (CDDAT3(CS)), R66.1, U1.79 (PC11)
TPS_ENABLE_B: J15.5, R28.2, U7.1 (EN/UVLO)
TPS_ENABLE_T: J13.5, U1.97 (PE0)
USB_DN: U1.70 (PA11), USB1.A7 (DN1), USB1.B7 (DN2)
USB_DP: U1.71 (PA12), USB1.A6 (DP1), USB1.B6 (DP2)
VBAT: J13.8, LED11.2 (A)
VBAT_B: C74.1, J15.8, R3.2, R23.1, U11.8 (VBUS), U11.10 (VIN+), U19.10 (VOUT), U19.11 (VOUT), U19.12 (VOUT), U19.13 (VOUT)
VBUS: C35.1, C77.1, D1.2 (A), LED2.2 (A), USB1.A4B9 (VBUS), USB1.B4A9 (VBUS)
VIDEO_IN: C41.1, J10.3, R83.1
VIDEO_OUT: R84.1, U17.7 (VIDEO)
VMOTORS: J13.9, LED12.2 (A)
VMOTORS_B: CN2.1, CN4.1, CN5.1, CN6.1, D2.2 (A), J15.9, R3.1, U11.9 (VIN-)
VOLTAGE_ADC_B: C28.2, J16.5, R23.2, R24.1
VOLTAGE_ADC_T: J14.5, U1.28 (PA4)
VSYS: C10.1, C78.1, D1.1 (K), J1.1, J1.3, J1.5, J1.7, J13.13, J18.7, J18.8, J18.9, J18.10, J18.11, J18.12, J18.13, J18.14, LED13.2 (A), U12.3 (VIN), U12.5 (EN)
VSYS_B: C3.2, C4.2, C5.2, C16.2, C27.2, D2.1 (K), J15.13, J20.7, J20.8, J20.9, J20.10, J20.11, J20.12, J20.13, J20.14, R7.1, U7.7 (VIN), U9.12 (VIN), U13.2
VTX_CH1: SW14.4 (B3), U17.6 (CH1)
VTX_CH2: SW14.5 (B2), U17.5 (CH2)
VTX_CH3: SW14.6 (B1), U17.4 (CH3)
VTX_SUPPLY: C36.2, C37.2, C38.2, J10.1, SW13.C, U5.3 (DVDD), U5.21 (AVDD), U5.24 (PVDD), U17.10 (VCC)
XTAL1: C40.2, U5.5 (CLKIN), U15.3
XTAL2: C39.1, U5.6 (XFB), U15.1

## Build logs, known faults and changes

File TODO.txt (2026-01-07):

1. Add sensor soft reset for recovery of communication (BMP580 and others)
2. Add pin headers besides connector for camera
3. Add battery health management system (monitor current across voltage decrease)

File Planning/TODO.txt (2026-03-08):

SOFTWARE

1. Add sensor soft reset for recovery of communication (BMP580 and others)
3. Add battery health management system in program (monitor current across voltage decrease)
5. Adaptive PID and vibration sensing. Log RPM and IMU data

HARDWARE

2. Add PCB module for receiver and display output.
3. MOVE ENTIRE PCB TO THE BOTTOM OF THE DRONE TO PUT GPS ON TOP.
4. See if LDOs can be used and redo power boosts/bucks to be safe

FINISH

1. Figure out necessary parts for order. 3x8 female headers, ribbon cable, VTX, etc
2. Add C6936314 FFC cable to order
3. Check all I2C addresses!!!

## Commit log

2025-12-31 Add PCB Files
    [Controller.kicad_pcb, Controller.kicad_sch]
2026-03-30 Enhance README with additional image and project details
    Added an additional image and expanded project description for the custom flight controller board, detailing its features and components.
